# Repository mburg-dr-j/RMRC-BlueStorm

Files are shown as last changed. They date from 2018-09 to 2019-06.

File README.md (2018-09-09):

# RMRC-BlueStorm
The RMRC-BlueStorm team is a group of Mercersburg students from around the world who come together to design a robot for the Rapidly Manufacured Robotics Competition

Logistical info: 

Team Name: Blue Storm RMRC 

Organization: Mercersburg Academy 

Country: USA 

Contact person: Marcus Jaiclin 

Email: jaiclinm@mercersburg.edu  

[NEXT](Directory)

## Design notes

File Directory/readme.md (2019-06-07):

# Directory Links

[2018 Competition](directory-links/2018-competition)

>A description and .stl of the final competition robot and any changes made during the competion

>A list of all the code used at the competition

>A description of challenges the robot faced

_________________________________________________________________________________________________________________________________________

[2019 competition](directory-links/2019-competition)

>A description of the physical desighn changes

>All code and changes in the code

>Any progress on other additions

_________________________________________________________________________________________________________________________________________

[Blog](directory-links/blog)

> A vague overview of the different items that we have been working on

>To learn more in depth about the projects desbribed in this section you can go to the the link with the corresponding time period 

_________________________________________________________________________________________________________________________________________

[Retired designs](directory-links/retired_designs)

> This is a list of all the designs that were used or had been in the prototype stages but were purged from the current design

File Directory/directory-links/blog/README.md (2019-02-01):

# Blog

**January 31st, 2019:**

>On this update you will see a list of every aspect of the design and components that was changed from the 2018 competition. If you wish to learn more about why and how an aspect was changed there will be an explanation of why it was changed and what benefits and disadvantages it provided in directory-links/2019-competiton-preparation/mechanical.

>>Thickness of the robot

>>Less Rounded corners

>>Motor Extrusions in each corner

>>Angled camera slots

>>Claw wheel design adjustment

>>Udoo X86 development board

>>Arm

>>CO2 sensor

>>Microphone array

>>Power Control Unit

>>Speaker

>>Dynamixel communication Board

>>Raspberry Pi 0

>>USB fish eye camera

>>USB 8 megapixel camera

>>External Ethernet Port

>>Dynamixel XM430W-350

**January 11th, 2019:**

>We were still unsatisfied with the speed of the XRDP Remote Desktop, and while having trouble connecting we searched for a new solution. We installed Ubuntu onto a mac, and open an ssh tunnel from the Ubuntu running the motors to the Ubuntu on the mac, using ssh -x (ip address) from the Mac to connect to the ubuntu. This worked phenomenally, with amazing fps running two cameras, although this is still through a wired connection. Furthermore, during the last update we were having trouble with the UDOO and having the Ubuntu side of the UDOO communicate with the Arduino side, as the Ubuntu was not seeing the Arduino as an output port to upload the code. We found [this guide](https://www.udoo.org/forum/threads/timeout-uploading-to-arduino-101.9891/#post-32686) that detailed a fix for it, and we were finally able to see the Arduino port. We have edited the motor code from last year, and now have a moving robot. Currently, Joseph is still working on finalizing the overall design of the robot, wiring, the positioning of the internal parts, more specifically the arm. Collin is now moving onto our sensors with our CO2 sensor and mic. Gary is still working on our hazmat recognition system, and the thermal camera. Joseph is still working with tkinter library, and beginning to create a GUI. 

>Sincerely,

>Blue-Storm RMRC

**December 12th, 2018:**

>We have switched our focus from VNC to [XRDP](https://help.ubuntu.com/community/xrdp) for setting up a remote desktop. We succesfully installed XRDP using [this](https://help.ubuntu.com/community/xrdp) link. We then installed guvcu, using [this](http://ubuntuhandbook.org/index.php/2018/10/guvcview-2-0-6-released-install-ubuntu/) link, to use as a streaming software for our two USB cameras (pictures below). once we played with the settings, it seemed to work rather well with minimal lag. Collins focus now is getting the motors working with the Udoo so that we can run some tests and pick our next motors. Joseph is starting to expirement with Graphical User Interfaces (GUI) to make start ups much faster and easier for everyone, we are thinking of using the tkinter library with python but if anyone else has had good results with others please let us know.

>Sincerely,

>Blue-Storm RMRC

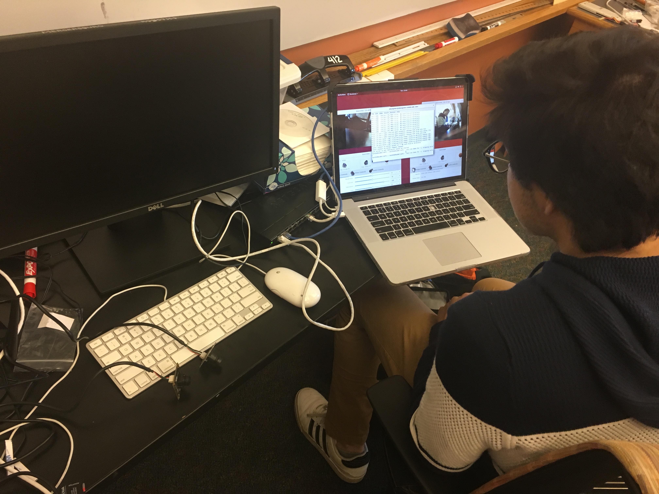
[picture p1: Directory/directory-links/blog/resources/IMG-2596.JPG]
software


**November 28th, 2018:**

>Gary, the newest member to our team. He is specializing in software, specifically machine learning and thermal imaging.

 >We are working on several projects at the moment. First, Collin is incorperating the [Udoo x86](https://www.udoo.org/udoo-x86/) into our robot to replace both of the raspberry pi's and the arduino. He will then implement [VNC](https://www.realvnc.com/en/connect/download/viewer/windows/) to remotly control the robot. Second Joseph is working on incorperating a compact arm into the robot. The arm will take a long time to develop and is still in the extremely early stages, but updates and designs will be posted periodically. Joseph is also working on adjusting the wheel design to be more effective on the hurdle course. Gary is working on a more reliable system for hazmat label recongnition.
 
>Once the robot is up and running again we are going to run tests to see whether speed or torque will be more valuable to the robot in the future. Depeding on the results of the test, we will upgrade to either the dynamixel [XM430W210T](http://support.robotis.com/en/product/actuator/dynamixel_x/xm_series/xm430-w210.htm), or the dynamixel XM430W350T.

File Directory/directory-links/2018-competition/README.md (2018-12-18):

# 2018 Competition

**[Team Description Materials(TDM)](2018-comp/TDP)**

>All information about the robot and sofware used in the 2018 Montreal competition

**[Software](2018-comp/software)**

>A list of the software used during the commpetition

**[Design](2018-comp/design)**

>A list of the .STLs used during the competition

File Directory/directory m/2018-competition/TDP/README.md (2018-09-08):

# TDP

**Logistical info**

>Team Name: RMRC BlueStorm

>Organisation: Mercersburg Academy

>Country: U.S.A.

>Contact person: Dr. Marcus Jaiclin

>Email:  jaiclinm@mercersburg.edu 

>Team website:

.

**Introduction summarising:**

>The team: Victor Li, 12th grade; Patrick Madden, 12th grade; Joseph Lieber, 11th grade; Marcus Jaiclin, Ph.D., Faculty mentor. 

>The technical aspects that it focuses on: Victor has been improving the image recognition algorithms. Patrick is working on the wireless communication and Joseph is working on improving the durability of the physical robot.

.

**System description, describing:**

>Hardware: The robot uses two Rasberry Pi model 3B+ to stream the two raberry Pi Cams and the thermal imaging camera, an arduino mega to control the 4 dynamixels (ax-12w). There is a speaker from a $1 gutted home phone that we bought in Montreal as well as a usb microphone connected to a Raspberry Pi.

>Software:

>Communications: The robot was able to communicate wirelessly through a 5ghz signal from our [router name], or it could be connected through two ethernat cable plugged into both Raspberry Pis.

>Human-robot interface: This was just a laptop that displayed the different programs while we used normal gaming keys(w,a,s,d) to control the robot.

.

**Application, describing:**

>Setup and packup of your robot and operator station:

>Mission strategy: 

>Experiments and testing that you have done or will do:

>How the particular strengths of your team are relevant to applications in the field:

**Conclusion, summarising:**

>What your team has learned so far:

>What you plan on doing between now and the competition:

.

**Appendix containing:**

>One table per robot outlining the components and estimated cost of your robot:

>At least one picture, 3D rendering or technical drawing of your robot:

>Be sure to highlight particular features of your robot:

>A list of software packages, hardware and electronic components that you have used, or plan to use, particularly those from the Open Source community, through the Open Academic Robot Kit or otherwise.

>A list of software packages, hardware and electronic components and designs that you have, or plan to, contribute to the Open Source community, through the Open Academic Robot Kit or otherwise.

>Note that you will still need to actually open source your components in the days prior to the competition as we assume you will continue development between the submission of the TDM and the competition!
References (to other work that you have made use of).

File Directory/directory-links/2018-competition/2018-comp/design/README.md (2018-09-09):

# Design

**[Main Body](RMRCmainbody5_0.stl)**

> This body was designed with durablity in mind. The body contain little to no corners, because this is where the stress fractures occur durring falls and other rough handling. The curved edges allow the stress to be distributed among a much greater surface area. This body was printed in "tough PLA" because this material is much more flexible than normal PLA, this allows the body itself to act as a suspension system when absoorbing shock and torgue from falls and other general use. 

>This body was printed on a makerbot Z18 3-D printer using the following settings:

>>             Temperature: 215 degrees C

>>     Chamber Temperature: 40 degrees C
 
>>            Layer Height: .1 MM

>>          Infill Density: 30%

>>          Infill Pattern: Hexagonal

>>            Travel Speed: 150 mm/s

>>        Number of Shells: 2

.

**[Claw Wheel](v1_1_claw_wheel.stl)**

>This style of wheel allows the robot to traverse hazzardous terrain with relative ease.The claw like style allows the wheel to dig an edge into the terrain and drag itself foward: so if one wheel gains traction the entire robot moves foward. The outside edges of the wheels are coated in [plastidip](https://smile.amazon.com/Plasti-Dip-Performix-12213-Black/dp/B00I9SK8XY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) to give the outer surface more traction.

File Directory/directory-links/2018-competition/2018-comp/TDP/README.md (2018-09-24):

# TDM

**Logistical info**

>Team Name: RMRC BlueStorm

>Organisation: Mercersburg Academy

>Country: U.S.A.

>Contact person: Dr. Marcus Jaiclin

>Email:  jaiclinm@mercersburg.edu 

>Team website: https://github.com/mburg-dr-j/RMRC-BlueStorm

.

**Introduction summarising:**

>The team: Victor Li, 12th grade; Patrick Madden, 12th grade; Joseph Lieber, 11th grade; Marcus Jaiclin, Ph.D., Faculty mentor. 

>The technical aspects that it focuses on: Victor has been improving the image recognition algorithms. Patrick is working on the wireless communication and Joseph is working on improving the durability of the physical robot.

.

**System description, describing:**

>Hardware: The robot uses two Rasberry Pi model 3B+ to stream the two raberry Pi Cams and the thermal imaging camera, an arduino mega to control the 4 dynamixels (ax-12a). There is a speaker from a $1 gutted home phone that we bought in Montreal as well as a usb microphone connected to a Raspberry Pi.

>Software: See files.  The basic setup was that the Laptop was connected via remote desktop (xrdp) to both Pis simultaneously, and then each Pi streamed video to a localhost website.  The operator could view one or both cameras using the two RDP connectons.  The Arduino was connected to one of the Pis through a USB, and communicated over a Serial channel.  The Pi ran a simple python code that transmitted the keystrokes, and the Arduino reacted to the keystrokes to control the motors.

>Communications: The robot was able to communicate wirelessly through a 5ghz signal from our router, or it could be connected through two ethernat cable plugged into both Raspberry Pis.

>Human-robot interface: This was just a laptop that displayed the different programs while we used normal gaming keys(w,a,s,d) to control the robot.

.

**Application, describing:**

>Setup and packup of your robot and operator station: The operator station was a laptop connected to a router connected to the robot. The robot consisted of 2 Raspberry Pis stacked on top of eachother. these were connected to an arduino mega that controlled the servos.

>Mission strategy: To be able to traverse the course the quickest while implementing as many imaging based sensor points possible

>Experiments and testing that you have done or will do: running the robot through home built courses. Testing the hazmat and motion tracking sensors using the online recources.

>How the particular strengths of your team are relevant to applications in the field: We are able to traverse enviroments very quickly and take a great deal of abuse. Perfect for time sensiive situations.

.

**Conclusion:**

>What your team has learned so far: We have learned that keeping the design simple is imperative to our success. Also that thouroughly testing every part of our robot in competition like circumstances is needed in order to be prepared at the competition.

.

**Appendix:**

 Component | Estimated Cost
 ----------|----------------
[arduino mega](https://www.robotshop.com/en/arduino-mega-2560-microcontroller-rev3.html)| $38
[3-cell(11.1V) Lipo Battery](https://www.amazon.com/gp/product/B000U2TPN6)|$24 each
[4 x Dynamixel AX-12A](https://www.trossenrobotics.com/p/ax-12w-dynamixel-robot-servo.aspx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)|$164.8
[Power Module](https://www.pololu.com/product/2574)|$14.95
[x2 Raspberry PI 3B+](https://www.adafruit.com/product/3775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)|$70
[PiCam](http://www.microcenter.com/product/465935/Raspberry_Pi_Camera_Module_V2?src=raspberrypi)|$24.99
[x2 Ethernet Cable](https://www.monoprice.com/product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)|$26
Router|(We just used a router that Dr. J had lying around his house.)
[FLIR Development Kit](https://www.sparkfun.com/products/13233)|$259
TOTAL: |$622.74

.

Open Source Hardware  

> The Arduino Mega

> The Raspberry Pi 3 and Pi cam

Open Source Software  

>Arduino IDE  

>‘ardyno’ library for Dynamixel servos on the Arduino. 

>Raspian operating system

References (to other work that you have made use of).

.

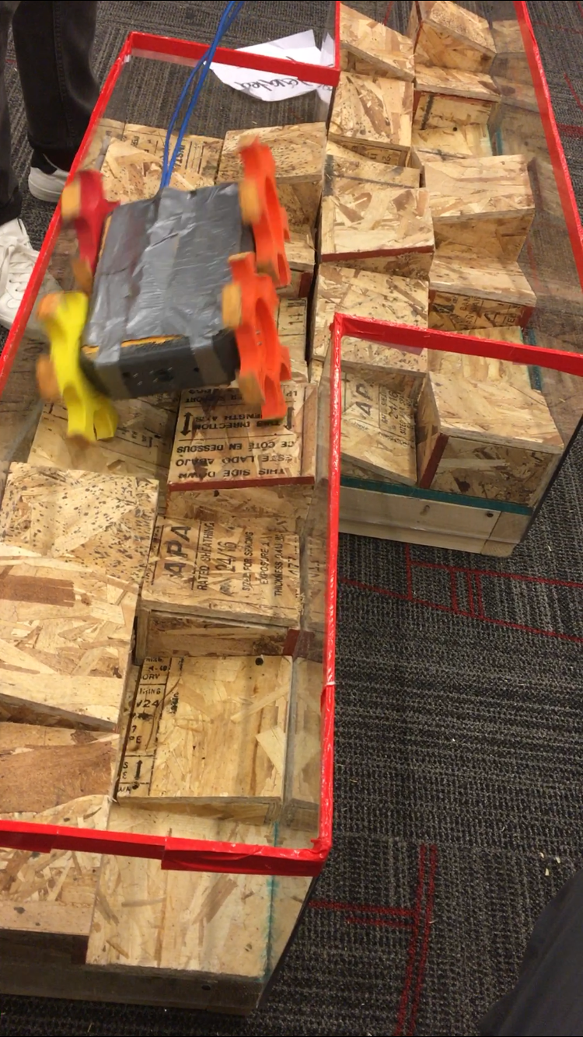
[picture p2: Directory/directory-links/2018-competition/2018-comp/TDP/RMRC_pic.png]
The Robot


.

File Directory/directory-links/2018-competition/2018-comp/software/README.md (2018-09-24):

# Software

[Mega Wheel](code/controllertomegawheelmode_ino.ino)

[Wirelessstandardreciever](code/wirelessstandardreceiverjuly24_ino.ino)

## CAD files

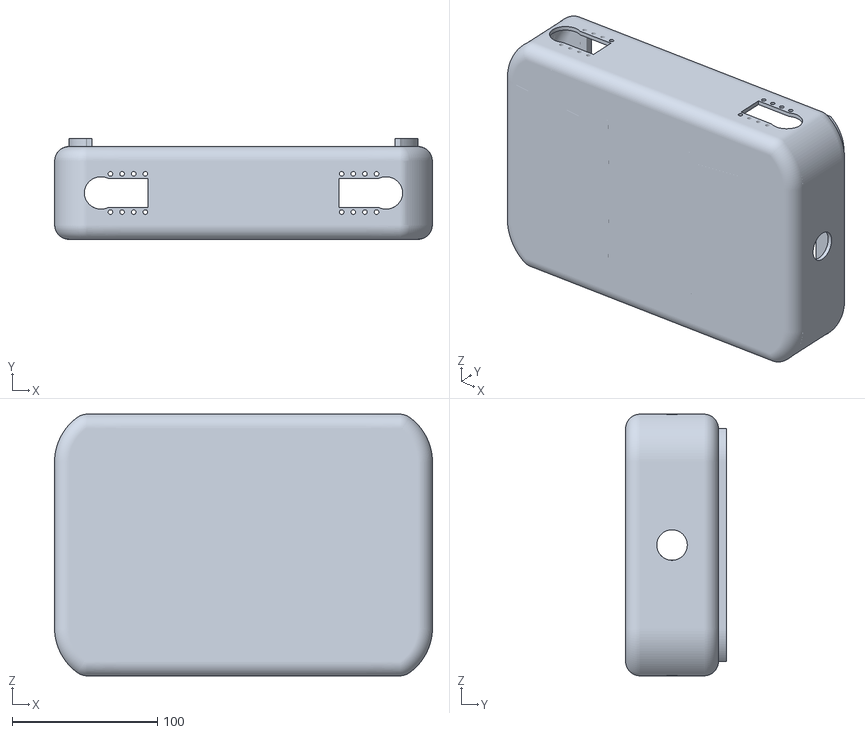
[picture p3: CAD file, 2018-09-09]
Directory/directory-links/2018-competition/2018-comp/design/RMRCmainbody5_0.stl
260.0 x 69.4 x 180.0

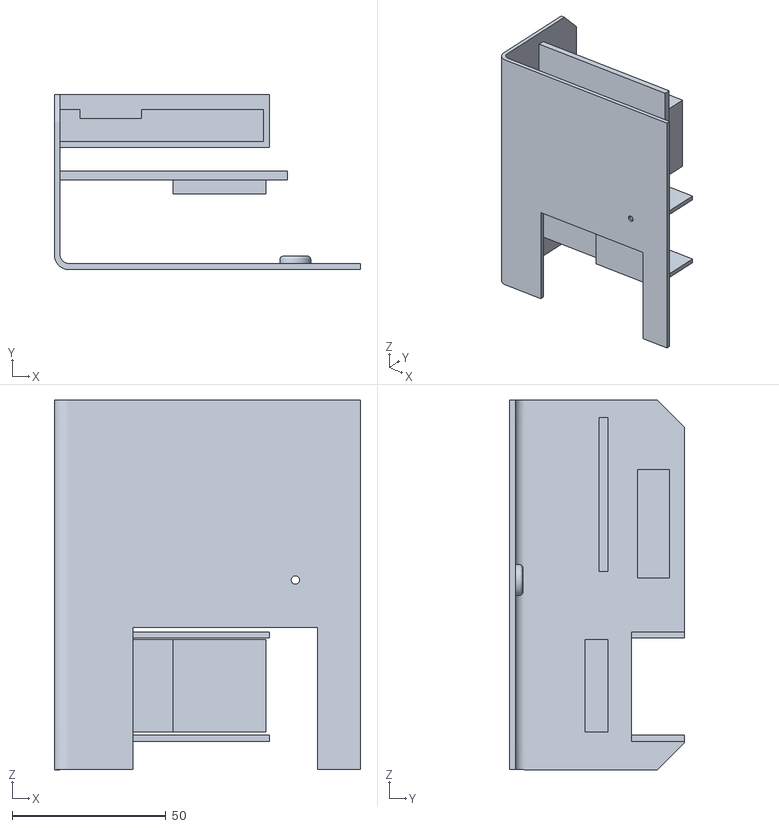
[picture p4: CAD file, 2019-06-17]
Directory/directory-links/2019-competition/Designs/circuitry_holder.stl
99.6 x 57.0 x 120.2

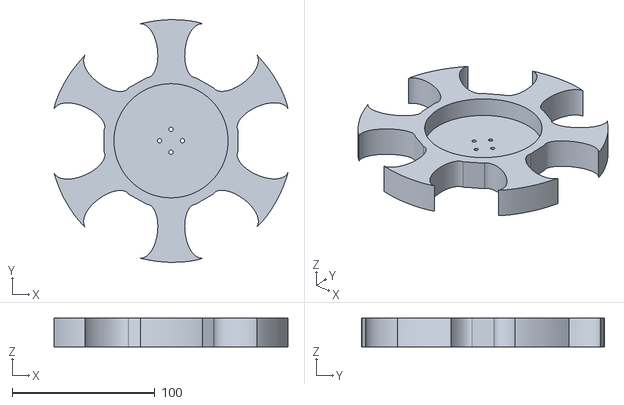
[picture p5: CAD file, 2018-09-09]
Directory/directory-links/2018-competition/2018-comp/design/v1_1_claw_wheel.stl
164.1 x 170.1 x 20.0

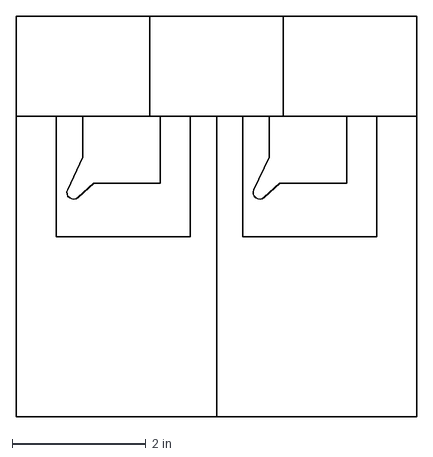
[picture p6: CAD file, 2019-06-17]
Directory/directory-links/2019-competition/Designs/Sorbothane_cuts.dxf
6.00 x 6.00 in

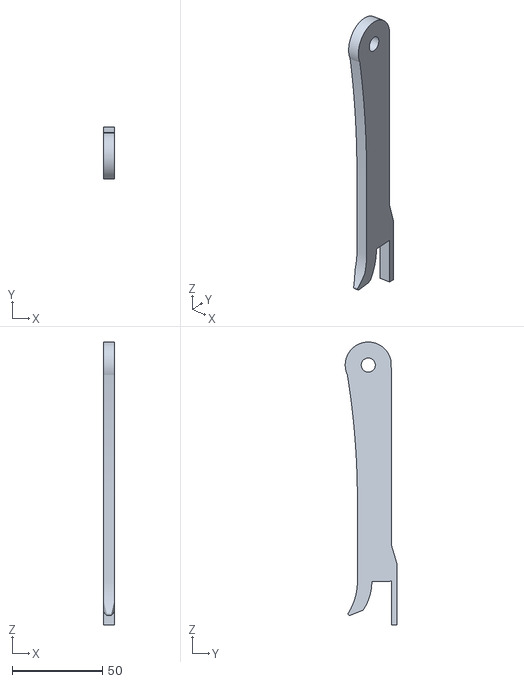
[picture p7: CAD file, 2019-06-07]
Directory/directory-links/2019-competition/Designs/forearm_mini.stl
6.20 x 28.6 x 156.5

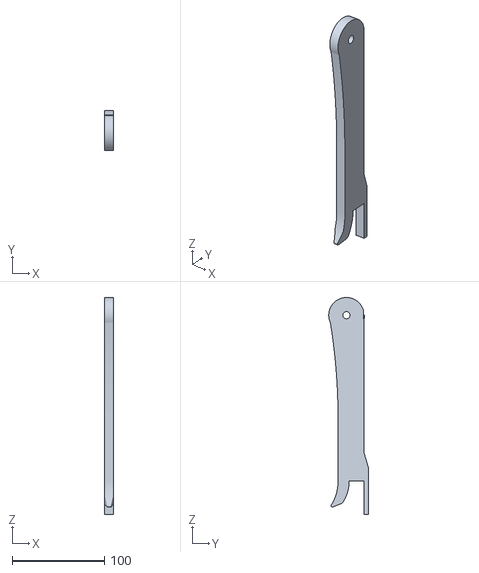
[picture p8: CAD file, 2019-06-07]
Directory/directory-links/2019-competition/Designs/controller_forearm.stl
9.30 x 42.8 x 234.8

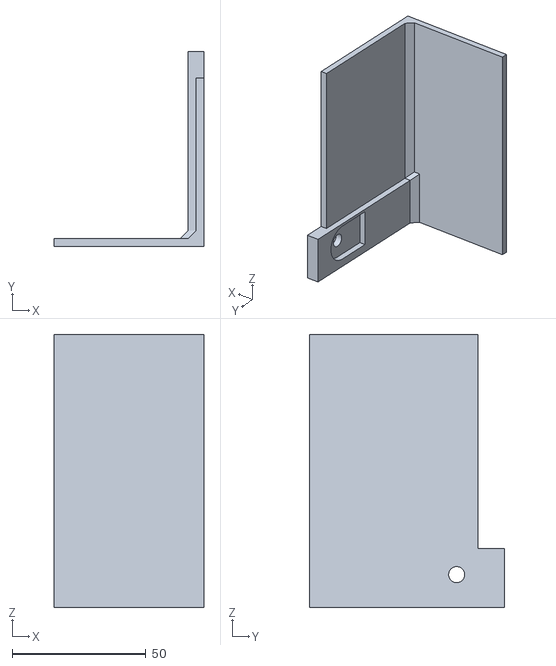
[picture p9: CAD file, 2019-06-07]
Directory/directory-links/2019-competition/Designs/controller_base.stl
56.0 x 73.0 x 102.0

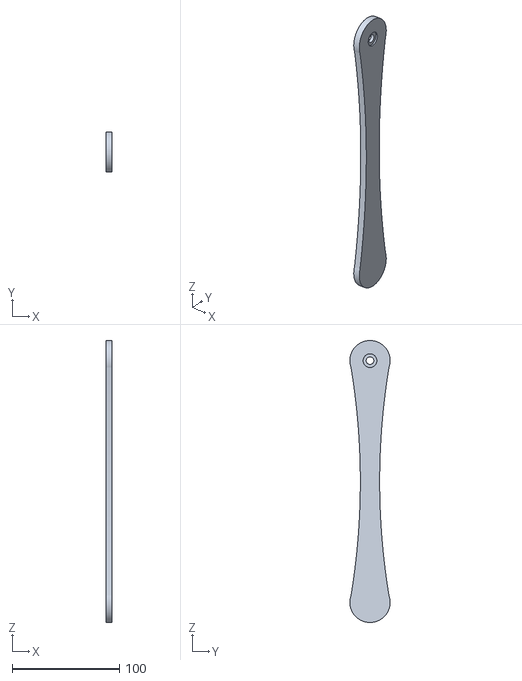
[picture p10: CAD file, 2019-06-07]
Directory/directory-links/2019-competition/Designs/controller_upper_arm.stl
6.00 x 37.5 x 262.5

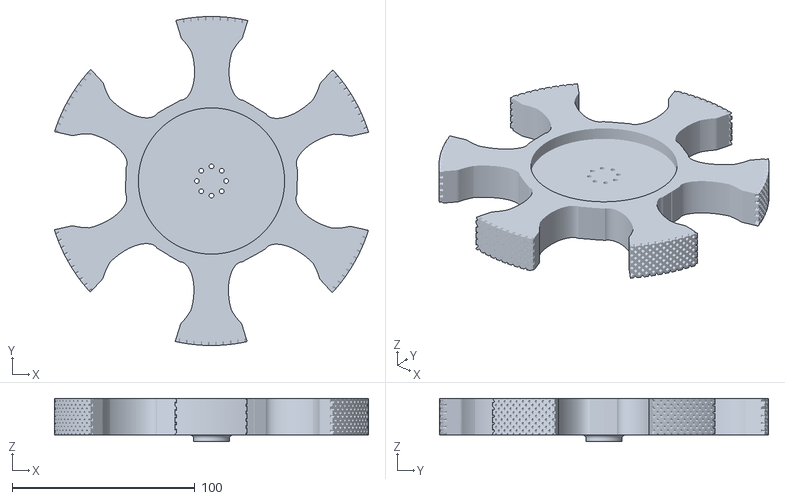
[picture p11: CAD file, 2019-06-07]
Directory/directory-links/2019-competition/Designs/v4_claw_wheel.stl
171.9 x 180.0 x 23.5

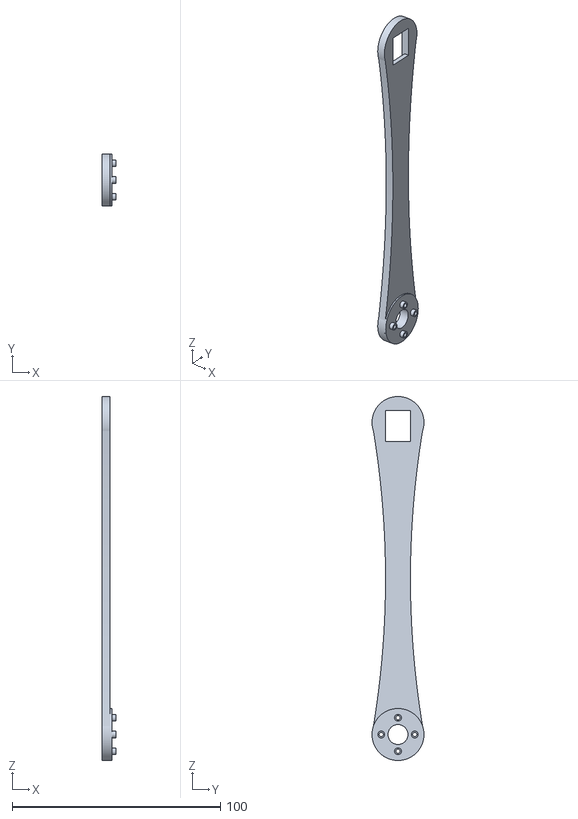
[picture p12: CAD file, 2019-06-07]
Directory/directory-links/2019-competition/Designs/upper_arm_mini.stl
6.81 x 25.0 x 175.0

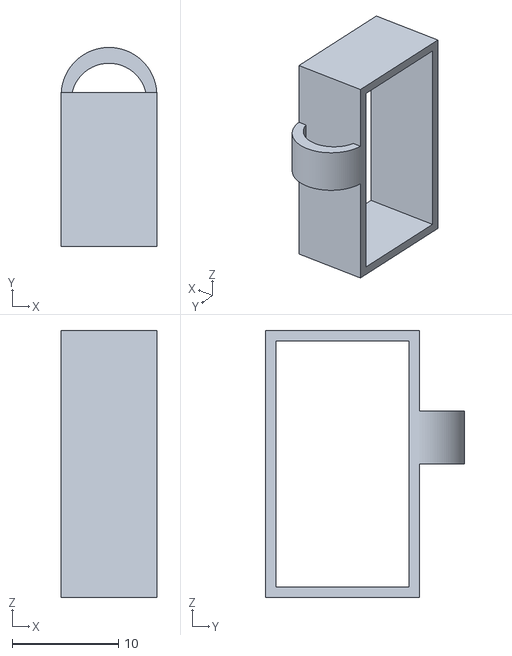
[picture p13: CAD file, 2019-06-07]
Directory/directory-links/2019-competition/Designs/elbow_wire_clip.stl
9.00 x 18.7 x 25.1

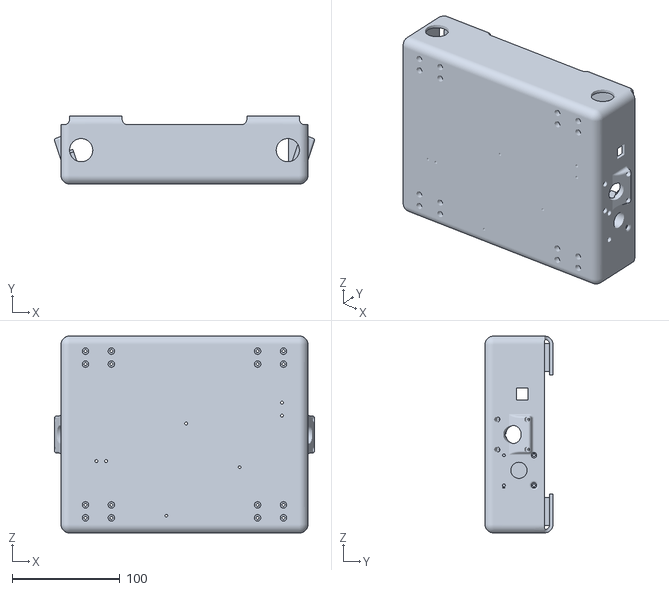
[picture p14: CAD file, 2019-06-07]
Directory/directory-links/2019-competition/Designs/v10_1(8mm extensions).stl
241.1 x 63.0 x 182.6

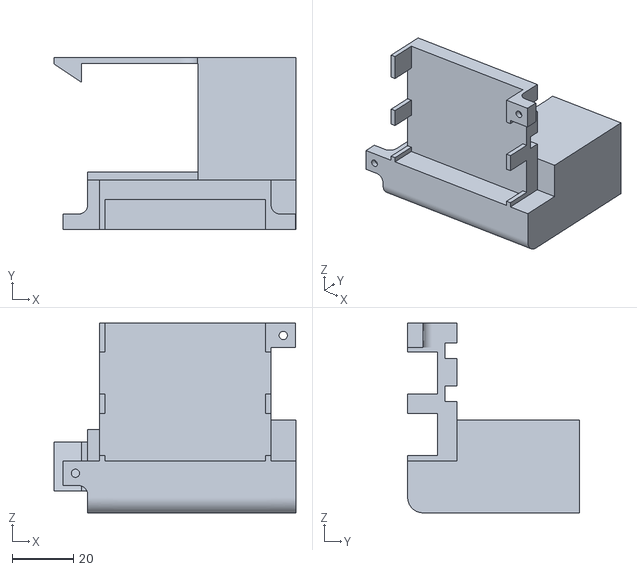
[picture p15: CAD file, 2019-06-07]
Directory/directory-links/2019-competition/Designs/battery_box.stl
79.0 x 56.0 x 61.9

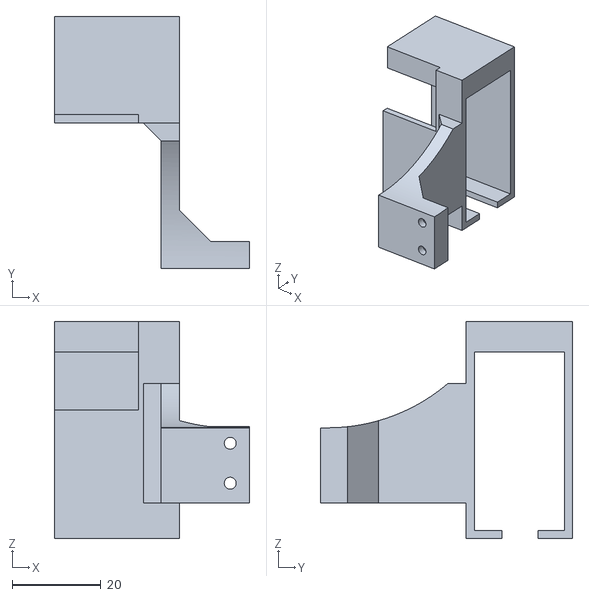
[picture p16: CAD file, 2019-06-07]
Directory/directory-links/2019-competition/Designs/ARM_holder.stl
44.1 x 56.9 x 49.0

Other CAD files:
Directory/directory-links/2019-competition/Designs/PCU_holder.stl
Directory/directory-links/2019-competition/Designs/old designs/battery_box.stl
Directory/directory-links/2019-competition/Designs/old designs/v8_1_4_RMRC_body.stl
Directory/directory-links/2019-competition/Designs/old designs/circuitry_holder.stl
Directory/directory-links/2019-competition/Designs/old designs/CO2_holder.stl
Directory/directory-links/2019-competition/Designs/old designs/prototype arm v30.step
Directory/directory-links/2019-competition/Designs/old designs/usb_hub_holder.stl
Directory/directory-links/2019-competition/Designs/old designs/v4_claw_wheel.stl

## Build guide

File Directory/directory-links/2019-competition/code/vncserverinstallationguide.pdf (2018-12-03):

Installing and configuring VNC -

First update the system with

Then install the xfce goodies

Set password for vncserver (8 characters max)

Create ~/.vnc/xstartup file so we can start the server

Insert following lines into file

Make the ~/.vnc/xstartup file executable

$ sudo apt update
$ sudo apt upgrade

$ sudo apt install vnc4server xfce xcfe-goodies

$ vncpasswd

$ mkdir ~.vnc
$ nano ~/.vnc/startup

#! /bin/bash

#xrdb ~/.xresources

def
export XKL_XMODMAP_DISABLE=1 unset SESSION_MANAGER
unset DBUS_SESSION_BUS_ADDRESS

startxfce &

$ chmod +x ~/.vnc/xstartup

Enable Screen Sharing -

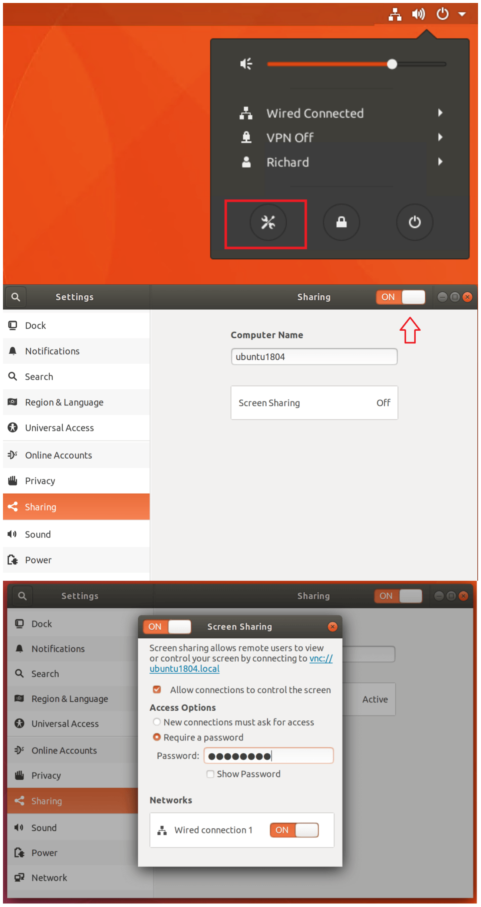
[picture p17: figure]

Making VNC run on startup -

Create a new file /etc/systemd/system/vncserver@.service using nano:

Insert the following lines while replacing the linuxconfig ZZZZZ username with username of your VNC user on Line 7 and Line 10:

Reload the Systemd:

Make the script run on reboot:

[Unit]
Description=Systemd VNC server startup script for Ubuntu 18.04 After=syslog.target network.target

[Service]
Type=forking
User= ZZZZZ
ExecStartPre=-/usr/bin/vncserver -kill :%i &> /dev/null ExecStart=/usr/bin/vncserver -depth 24 -geometry 1440x900 :%i PIDFile=/home/ZZZZZ/.vnc/%H:%i.pid ExecStop=/usr/bin/vncserver -kill :%i

[Install]
WantedBy=multi-user.target

$ sudo nano /etc/systemd/system/vncserver@.service

$ sudo systemctl daemon-reload

$ sudo systemctl enable vncserver@1

To start VNC desktop, enter:

To stop VNC desktop, enter:

$ sudo service vncserver@1 start

$ sudo service vncserver@1 stop

Sites used -
https://linuxconfig.org/vnc-server-on-ubuntu-18-04-bionic-beaver-linux

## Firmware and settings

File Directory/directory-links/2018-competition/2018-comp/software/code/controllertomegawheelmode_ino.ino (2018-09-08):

/*                                          __                    
   ____ ___  ___  _____________  __________/ /_  __  ___________ _
  / __ `__ \/ _ \/ ___/ ___/ _ \/ ___/ ___/ __ \/ / / / ___/ __ `/
 / / / / / /  __/ /  / /__/  __/ /  (__  ) /_/ / /_/ / /  / /_/ / 
/_/ /_/ /_/\___/ /   \___/\/_// /  /____/_.___/\__,_/_/   \__, /  
   _________  / /_  ____  / /_(_)_________               /____/   
  / ___/ __ \/ __ \/ __ \/ __/ / ___/ ___/                        
 / /  / /_/ / /_/ / /_/ / /_/ / /__(__  )                         
/_/   \____/_.___/\____/\__/_/\___/____/ 

Victor Li '18, Maddie Rogers '17, Pat Madden '18, 2017
Powered by nihilism, coffee, and some curiosity 
*/

//FOR USE WITH TETHER 

//---! XBee incompatible, use only with USB shield on mega  
//---! for direct communication between controller and mega (requires an arduino with USB shield and PS4 controller)

// ---! Code presented is heavily modifed from the example
// ---! sketch for the PS4 USB library - developed by Kristian Lauszus
// ---! For more information visit his blog: http://blog.tkjelectronics.dk/ 

// ---! I tried to write this as cleanly as I could, though
// ---!  if you have any questions I can be reached at patrickvincentmadden@gmail.com 

#include <PS4USB.h>
#include <usbhub.h>
#include <PS4Parser.h>

#include <Dynamixel.h>
#include <DynamixelConsole.h>
#include <DynamixelInterface.h>
#include <DynamixelMotor.h>

// Satisfy the IDE, which needs to see the include statment in the ino too.
#ifdef dobogusinclude
#include <spi4teensy3.h>
#include <SPI.h>
#endif

USB Usb;
PS4USB PS4(&Usb);

char myArray[100];
int i=0;
String str;
byte incoming=0;

int speedSelect = 1; //default set speedA -> speedB -> speedC -> speedA ...

int speedA = 750;
int speedB = 1000;
int speedC = 150;

int a = 0;
int b = 50; //hack value, turning right or left on very low speeds (like 150) lowers torque intolerably so this should help

int invert = 1; //default set NO
bool inverted = false;

DynamixelInterface &interface=*createSerialInterface(Serial);
DynamixelMotor motor1(interface, 55);
DynamixelMotor motor2(interface, 54);
DynamixelMotor motor3(interface, 60);
DynamixelMotor motor4(interface, 58);

void forward() {
  switch(speedSelect) {
     case 1:
      Serial.print("case 1");
      motor1.speed(speedA);
      motor2.speed(-speedA);
      motor3.speed(speedA);
      motor4.speed(-speedA);  
     break;
     case 2:
      Serial.print("case 2");
      motor1.speed(speedB);
      motor2.speed(-speedB);
      motor3.speed(speedB);
      motor4.speed(-speedB);
     break;
     case 3:
      Serial.print("case 3");
      motor1.speed(speedC);
      motor2.speed(-speedC);
      motor3.speed(speedC);
      motor4.speed(-speedC);
     break;
    }
}
void backward() {
  switch(speedSelect) {
     case 1:
     Serial.print("case 1");
      motor1.speed(-speedA);
      motor2.speed(speedA);
      motor3.speed(-speedA);
      motor4.speed(speedA);  
     break;
     case 2:
      Serial.print("case 2");
      motor1.speed(-speedB);
      motor2.speed(speedB);
      motor3.speed(-speedB);
      motor4.speed(speedB);
     break;
     case 3:
      Serial.print("case 3");
      motor1.speed(-speedC);
      motor2.speed(speedC);
      motor3.speed(-speedC);
      motor4.speed(speedC);
     break;
    }
}
void right() {
  switch(speedSelect) {
     case 1:
      Serial.print("case 1");
      motor1.speed(speedA);
      motor2.speed(speedA);
      motor3.speed(speedA);
      motor4.speed(speedA);  
     break;
     case 2:
      Serial.print("case 2");
      motor1.speed(speedB);
      motor2.speed(speedB);
      motor3.speed(speedB);
      motor4.speed(speedB);
     break;
     case 3:
      Serial.print("case 3");
      motor1.speed(speedC+b);
      motor2.speed(speedC+b);
      motor3.speed(speedC+b);
      motor4.speed(speedC+b);
     break;
    }
}
void left() {
  switch(speedSelect) {
     case 1:
     Serial.print("case 1");
      motor1.speed(-speedA);
      motor2.speed(-speedA);
      motor3.speed(-speedA);
      motor4.speed(-speedA);  
     break;
     case 2:
      Serial.print("case 2");
      motor1.speed(-speedB);
      motor2.speed(-speedB);
      motor3.speed(-speedB);
      motor4.speed(-speedB);
     break;
     case 3:
      Serial.print("case 3");
      motor1.speed(-speedC-b);
      motor2.speed(-speedC-b);
      motor3.speed(-speedC-b);
      motor4.speed(-speedC-b);
     break;
    }
}

void north() {
  switch(invert){
    case 1:
      forward();  
    break;
    case 2:
      backward();  
    break;
    default:
    //empty
    break;
  }  
}
void south() {
  switch(invert){
    case 1:
      backward();  
    break;
    case 2:
      forward();  
    break;
    default:
    //empty
    break;
  }    
}
// changes made here, if issues switch back to original
void east() {
  switch(invert){
    case 1:
      right();  
    break;
    case 2:
      right(); // left();
    break;
    default:
    //empty
    break;
  }   
}
void west() {
  switch(invert){
    case 1:
      left();  
    break;
    case 2:
      left(); // right();
    break;
    default:
    //empty
    break;
  }   
}
// end changes made

void setup() {
  Serial.begin(57600);
  interface.begin(1000000);
#if !defined(__MIPSEL__)
  while (!Serial); // Wait for serial port to connect - used on Leonardo, Teensy and other boards with built-in USB CDC serial connection
#endif
  if (Usb.Init() == -1) {
    //Serial.print(F("\r\nOSC did not start"));
    while (1); // Halt
  }
  delay(100);
    motor1.jointMode();
    motor2.jointMode();
    motor3.jointMode();
    motor4.jointMode();
  delay(100);
    while (! Serial) {
    delay(1);
  }
    motor1.position(a);
    motor2.position(a);
    motor3.position(a);
    motor4.position(a);
  delay(100);
    motor1.wheelMode();
    motor2.wheelMode();
    motor3.wheelMode();
    motor4.wheelMode();
  delay(100);
    while (! Serial) {
    delay(1);
  }
}

void loop() {
  Usb.Task();
  if (PS4.connected()) {
    if (PS4.getButtonClick(UP)) {
      Serial.println("hit");        
      north();
    }
    if (PS4.getButtonClick(RIGHT)) {
      Serial.println("hit");
      east();
    }
    if (PS4.getButtonClick(DOWN)) {
      Serial.println("hit");
      south();  
    }
    if (PS4.getButtonClick(LEFT)) {
      Serial.println("hit");
      west();
    }
    if (PS4.getButtonClick(CROSS)) {
      Serial.println("hit");
      motor1.speed(0);
      motor2.speed(0);
      motor3.speed(0);
      motor4.speed(0);
      motor1.speed(0);
      motor2.speed(0);
      motor3.speed(0);
      motor4.speed(0);
    }
    if (PS4.getButtonClick(SQUARE)) {
      Serial.println("hit");
      if(inverted)
      {
        invert = 1;
        inverted = false;
        Serial.print("invert = ");
        Serial.println(invert); 
      }else 
      {
        invert = 2;
        inverted = true;
        Serial.print("invert = ");
        Serial.println(invert);
      }
    }
    if (PS4.getButtonClick(TRIANGLE)) {
      Serial.println("hit");
      if(speedSelect==3)
      {
        speedSelect = 1;
        Serial.print(speedSelect);
      }else
      {
        speedSelect++;
        Serial.print(speedSelect);  
      }
    }
//    if (PS4.getButtonClick(CIRCLE) {

//    }
  }
}

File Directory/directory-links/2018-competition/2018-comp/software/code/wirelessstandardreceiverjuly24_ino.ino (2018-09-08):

/*                                          __                    
   ____ ___  ___  _____________  __________/ /_  __  ___________ _
  / __ `__ \/ _ \/ ___/ ___/ _ \/ ___/ ___/ __ \/ / / / ___/ __ `/
 / / / / / /  __/ /  / /__/  __/ /  (__  ) /_/ / /_/ / /  / /_/ / 
/_/ /_/ /_/\___/ /   \___/\/_// /  /____/_.___/\__,_/_/   \__, /  
   _________  / /_  ____  / /_(_)_________               /____/   
  / ___/ __ \/ __ \/ __ \/ __/ / ___/ ___/                        
 / /  / /_/ / /_/ / /_/ / /_/ / /__(__  )                         
/_/   \____/_.___/\____/\__/_/\___/____/ 

Victor Li '18, Maddie Rogers '17, Pat Madden '18
Mentored by Conner Caruso '16 and Dr. J 2017
Powered by nihilism, coffee, and some curiosity 
*/

// ---! Compatible with wirelessStandardSENDERJuly24  
// ---! for wireless communication between XBees      
// ---! Requires one XBee with USB shield (attached to PS4
// ---! controller), and one XBee receiver on chassis
// ---! default start is on wheelMode                

// ---! Code presented is heavily modifed from the example
// ---! sketch for the PS4 USB library - developed by Kristian Lauszus
// ---! For more information visit his blog: http://blog.tkjelectronics.dk/ 

// ---! I tried to write this as cleanly as I could, though
// ---!  if you have any questions I can be reached at patrickvincentmadden@gmail.com 

// ---! The untested, experimental part of this is the addition of jointMode control,
// ---!  which in theory will give the driver further accuracy in navigation
// ---!  although it will require extensive testing as I'm unsure how it'll work (july24)               !---
           
// SoftwareSerial to communicate with the XBee:
#include <SoftwareSerial.h>
// XBee's DOUT (TX) is connected to pin 2 (Arduino's Software RX)
// XBee's DIN (RX) is connected to pin 3 (Arduino's Software TX)
SoftwareSerial XBee(52, 3); // RX, TX

#include <Dynamixel.h>
#include <DynamixelConsole.h>
#include <DynamixelInterface.h>
#include <DynamixelMotor.h>

char myArray[100];
int i=0;
String str;
byte incoming=0;

int a = 0; //angle for motor position in jointMode
int angleIncrement = 2;

int invert = 1; //default set NO
bool inverted = false;

bool wheel;    

int speedSelect = 1; //intial set: speedA

int speedA = 750;
int speedB = 1000;
int speedC = 200;

DynamixelInterface &interface=*createSerialInterface(Serial2);
DynamixelMotor motor1(interface, 55);
DynamixelMotor motor2(interface, 61);
DynamixelMotor motor3(interface, 60);
DynamixelMotor motor4(interface, 58);

void setup() {
  XBee.begin(57600);
  //Serial.begin(57600);
  interface.begin(1000000);
  delay(10);
    motor1.jointMode();
    motor2.jointMode();
    motor3.jointMode();
    motor4.jointMode();
  delay(10);
    motor1.position(a);
    motor2.position(a);
    motor3.position(a);
    motor4.position(a);
  delay(10);
    motor1.wheelMode();
    motor2.wheelMode();
    motor3.wheelMode();
    motor4.wheelMode();
  delay(10);
    while (! Serial) {
    delay(1);
  }
}

//for jointMode
void jointNorth() {
    switch(invert)
    {
      case1:
        motor1.position(a);
        motor2.position(-a);
        motor3.position(a);
        motor4.position(-a);
      break;
      case2:
        motor1.position(-a);
        motor2.position(a);
        motor3.position(-a);
        motor4.position(a);      
      break;
    }
}
void jointSouth() {
    switch(invert)
    {
      case1:
        motor1.position(-a);
        motor2.position(a);
        motor3.position(-a);
        motor4.position(a);
      break;
      case2:
        motor1.position(a);
        motor2.position(-a);
        motor3.position(a);
        motor4.position(-a);      
      break;
    }
}
void jointRight() {
    motor1.position(a);
    motor2.position(a);
    motor3.position(a);
    motor4.position(a);
}
void jointLeft() {
    motor1.position(-a);
    motor2.position(-a);
    motor3.position(-a);
    motor4.position(-a);
}

//for wheelMode
void wheelForward() {
  switch(speedSelect) {
     case 1:
      //Serial.print("case 1");
      motor1.speed(speedA);
      motor2.speed(-speedA);
      motor3.speed(speedA);
      motor4.speed(-speedA);  
     break;
     case 2:
      //Serial.print("case 2");
      motor1.speed(speedB);
      motor2.speed(-speedB);
      motor3.speed(speedB);
      motor4.speed(-speedB);
     break;
     case 3:
      //Serial.print("case 3");
      motor1.speed(speedC);
      motor2.speed(-speedC);
      motor3.speed(speedC);
      motor4.speed(-speedC);
     break;
    }
}
void wheelBackward() {
  switch(speedSelect) {
     case 1:
     ///Serial.print("case 1");
      motor1.speed(-speedA);
      motor2.speed(speedA);
      motor3.speed(-speedA);
      motor4.speed(speedA);  
     break;
     case 2:
      //Serial.print("case 2");
      motor1.speed(-speedB);
      motor2.speed(speedB);
      motor3.speed(-speedB);
      motor4.speed(speedB);
     break;
     case 3:
      //Serial.print("case 3");
      motor1.speed(-speedC);
      motor2.speed(speedC);
      motor3.speed(-speedC);
      motor4.speed(speedC);
     break;
    }
}
void wheelRight() {
  switch(speedSelect) {
     case 1:
      //Serial.print("case 1");
      motor1.speed(speedA);
      motor2.speed(speedA);
      motor3.speed(speedA);
      motor4.speed(speedA);  
     break;
     case 2:
      //Serial.print("case 2");
      motor1.speed(speedB);
      motor2.speed(speedB);
      motor3.speed(speedB);
      motor4.speed(speedB);
     break;
     case 3:
      //Serial.print("case 3");
      motor1.speed(speedC);
      motor2.speed(speedC);
      motor3.speed(speedC);
      motor4.speed(speedC);
     break;
    }
}
void wheelLeft() {
  switch(speedSelect) {
     case 1:
     //Serial.print("case 1");
      motor1.speed(-speedA);
      motor2.speed(-speedA);
      motor3.speed(-speedA);
      motor4.speed(-speedA);  
     break;
     case 2:
      //Serial.print("case 2");
      motor1.speed(-speedB);
      motor2.speed(-speedB);
      motor3.speed(-speedB);
      motor4.speed(-speedB);
     break;
     case 3:
      //Serial.print("case 3");
      motor1.speed(-speedC);
      motor2.speed(-speedC);
      motor3.speed(-speedC);
      motor4.speed(-speedC);
     break;
    }
}

void wheelNorth() {
  switch(invert){
    case 1:
      wheelForward();  
    break;
    case 2:
      wheelBackward();  
    break;
    default:
    //empty
    break;
  }  
}
void wheelSouth() {
  switch(invert){
    case 1:
      wheelBackward();  
    break;
    case 2:
      wheelForward();  
    break;
    default:
    //empty
    break;
  }    
}
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

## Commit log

2018-09-08 fixing folder names 9-07-18
    [controllertomegawheelmode_ino.ino, wirelessstandardreceiverjuly24_ino.ino]
2018-09-08 Revert "revert 9-08-18 2:52"
    This reverts commit b79eefbd6e862871f1255d939c28309ab1b1b647.
    [controllertomegawheelmode_ino.ino, wirelessstandardreceiverjuly24_ino.ino]
2018-09-09 9-08-18 10:20
    [RMRCmainbody5_0.stl, v1_1_claw_wheel.stl]
2018-09-09 adding stls
    [RMRC_body_v6_2.stl, v1_1_arduino_box.stl, v1_1_dynamixel_heat_sink.stl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]
2018-09-09 organizing stls
    [RMRC_body_v6_2.stl, v1_1_arduino_box.stl, v1_1_dynamixel_heat_sink.stl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]
2018-09-13 9-13-18 9:13
    [RMRC_body_v6_2.stl, RMRCmainbody5_0.stl, v1_1_arduino_box.stl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]
2018-09-13 9-13-18 9:17
    [RMRC_body_v6_2.stl, v1_1_arduino_box.stl, v1_1_dynamixel_heat_sink.stl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]
2018-10-29 new body designs
    [v7.2_body_RMRC.stl, v7.3_body_RMRC.stl, v7_4_body_RMRC.stl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]
2019-02-13 deleting old designs
    [RMRC_body_v6_2.stl, v1_1_arduino_box.stl, v1_1_dynamixel_heat_sink.stl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]
2019-02-13 adding new designs
    [CO2_holder.stl, PCU_holder.stl, battery_box.stl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]
2019-06-07 re organize
    [ARM_holder.stl, CO2_holder.stl, PCU_holder.stl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]
